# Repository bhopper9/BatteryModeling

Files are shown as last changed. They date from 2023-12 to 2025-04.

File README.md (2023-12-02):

Rensselaer Motorsport Battery Models

This respository currently contains two major projects:

RM26 Project - This was the final battery design for RM26 (2022-2023 competition car).
WIP RM27 Project - This is the most up to date battery design for RM27 (2023-2024 competition car).

Most of the circuits are made using KiCad or LTSpice, both free for download on the internet.

Additional schematics and drawings are from the manufacturer of components or made in Microsoft Visio.

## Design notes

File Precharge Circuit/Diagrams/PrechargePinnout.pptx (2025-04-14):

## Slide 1

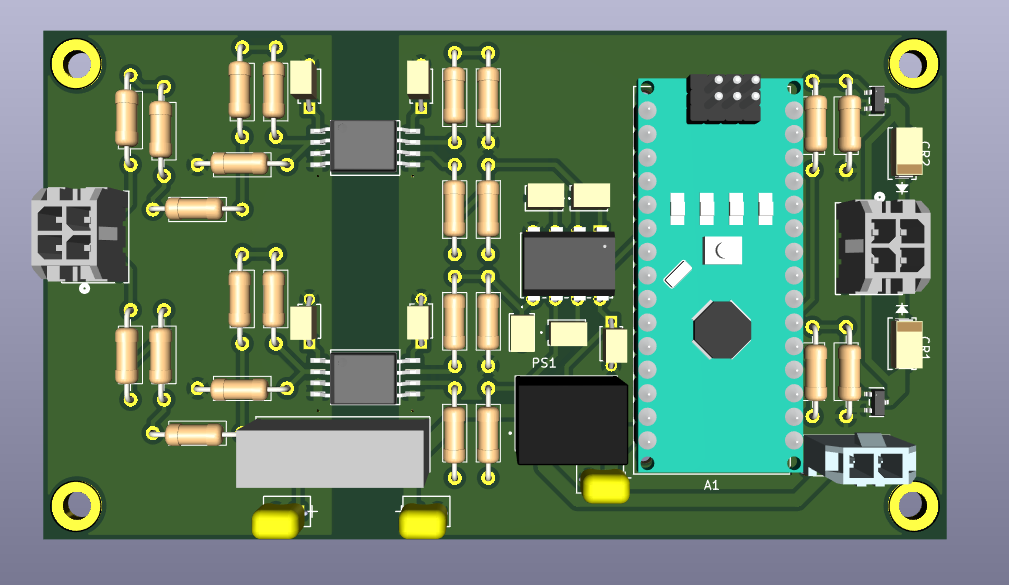
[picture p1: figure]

Relay

SHD IN

VInv

HV GND

VBatt

GND

AIR

V+
(Battery or 12V)

GND

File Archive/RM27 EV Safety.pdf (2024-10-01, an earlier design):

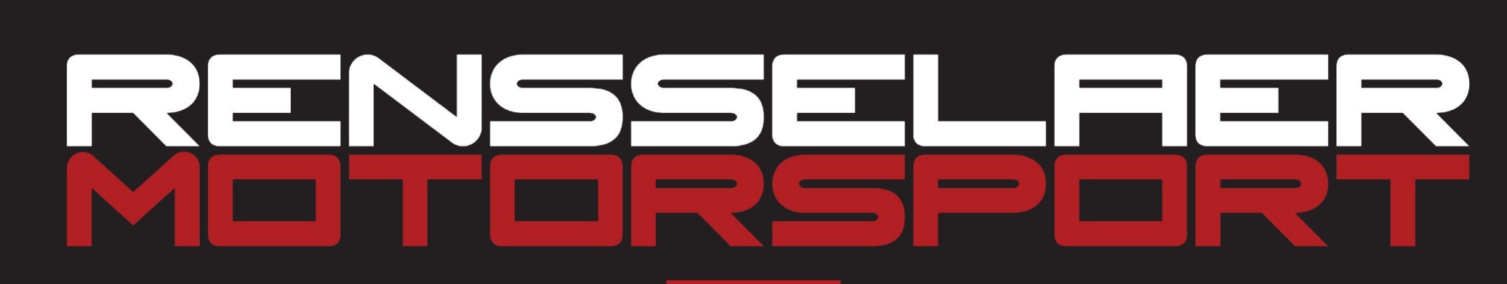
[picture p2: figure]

# Electrical Safety

Sean Trimper - ESO
trimps@rpi.edu - (603)204-0353 December 6, 2023

## - Gain basic knowledge of electrical safety including:

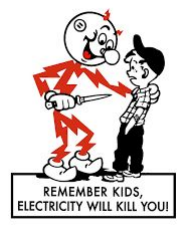
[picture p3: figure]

## a. Battery cells

## b. Powertrain

## c. HV System

## d. LV System

## e. Shutdown system

## f. Equipment

## Goal

- Damaged cells should be reported and handled with extreme care
- Cell wrapping is not just used to change how the cell looks
– | It insulates the positive and negative terminal
– | Even a slight nick in the wrapping will increase the chances of an
| accidental short between the terminals
- Individual cells are capable of high current output
- Misuse or a short between terminals can cause fire or an explosion
- The cells will be hot
- Thermal runaway is when a cell overheats and domino effects the

accumulator (why EV fires are BAD)
- If handling cells, contact ESO

## Battery Cells

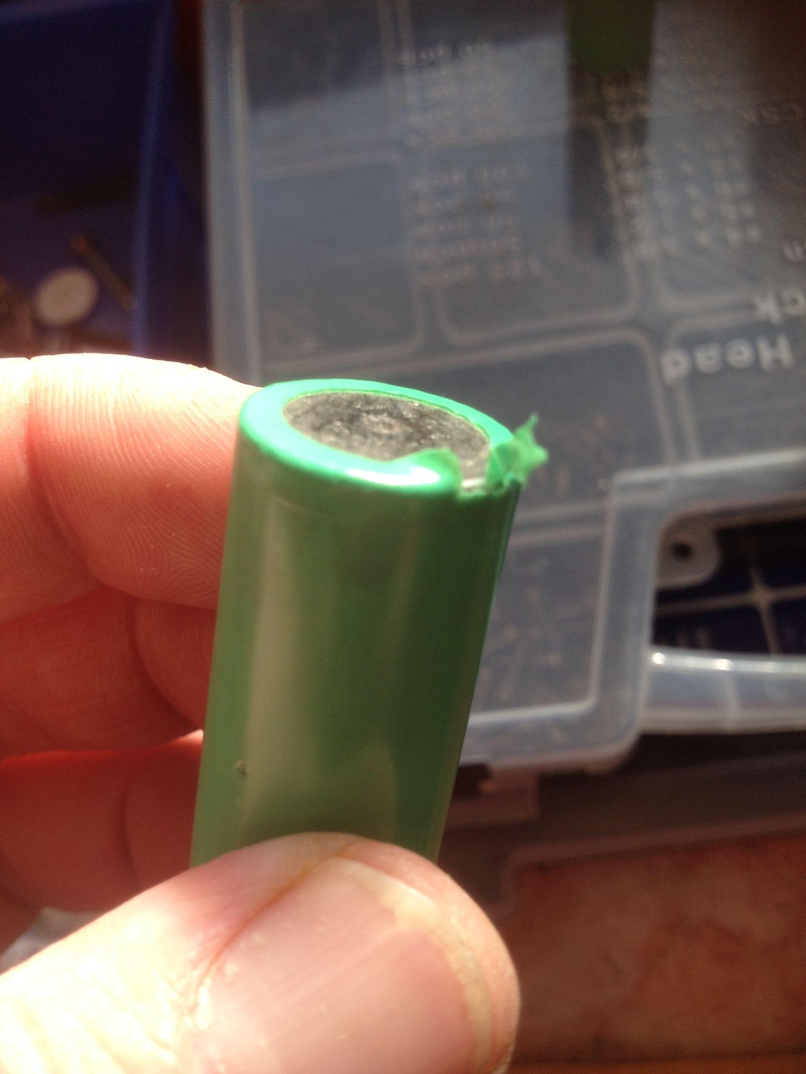
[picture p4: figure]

https://www.osha.gov/sites/default/files/publications/shib011819.pdf

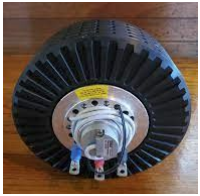
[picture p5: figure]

- In addition to being connected to 400V, the motor is heavy and

moving (and EXPENSIVE)

- The entire motor casing spins FAST
- Even if the motor has stopped moving:
- Ensure power is cut off from the tractive system

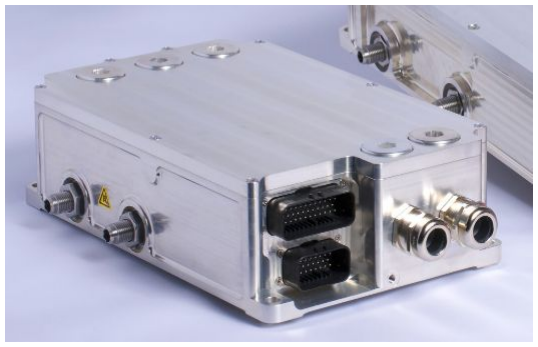
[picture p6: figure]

- Motor will be hot
- The ESC handles many volts and amps
- ESC will be hot
- If handling motor or ESC, contact PT Lead or ESO

## Powertrain

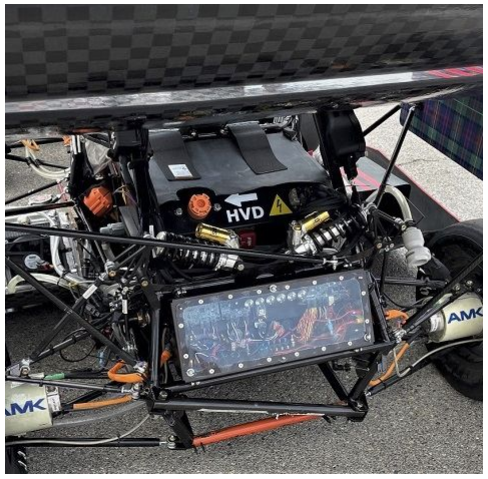
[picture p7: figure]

- There are many built in safety mechanisms within the

accumulator

- If something does go wrong
- High Voltage Disconnect (HVD)
– | There will be an HVD on the car
– | HVD labeled “HVD” and in rear of car
– | PULL MAIN HVD IF DRIVER IN DANGER
- Isolation
– | The battery segments will be isolated from the other
| components in the accumulator
– | Added layer of protection
– | Will make an LED light up colors depending on status

## HV System

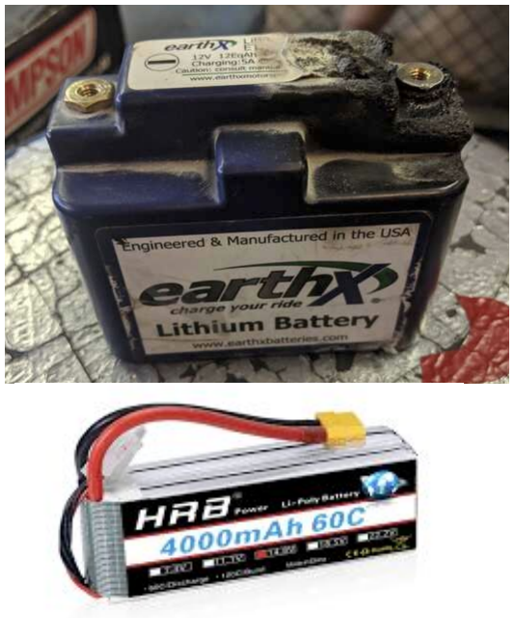
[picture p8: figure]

### - Biggest safety concern is the LV Battery

- Relatively low voltage, but extremely high current
- Ask LV lead or ESO before handeling
- Store in a dry and cool location
- Most common mistake: Shorting cell terminals
– | Overheats and will cause fire
– | THIS HAS HAPPENED TO US BEFORE!!!

### - 12V and 5V systems

- Can short if loose pwr and gnds

– Cover with E-tape

- Has indicator lights

## LV System

## EV Indicator Lights

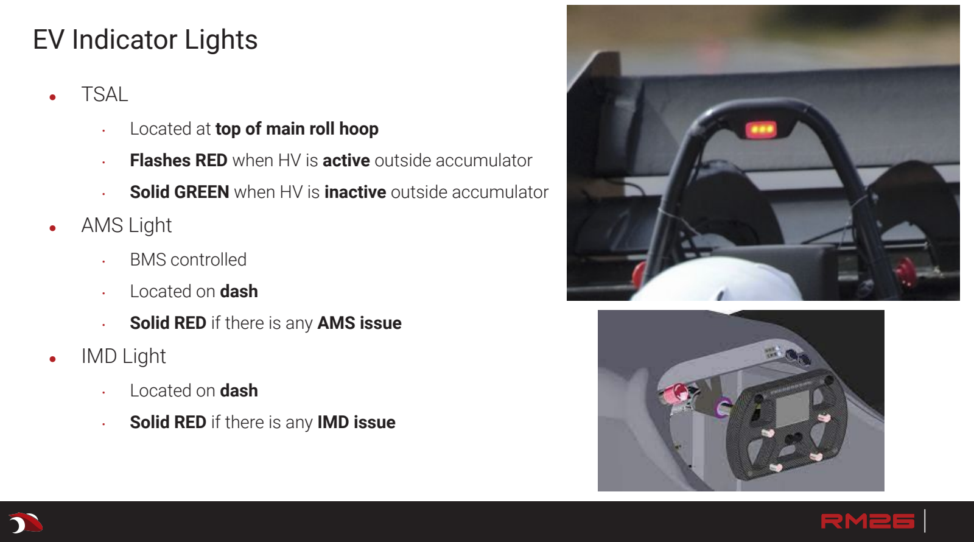
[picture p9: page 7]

- TSAL
- Located at top of main roll hoop
- Flashes RED when HV is active outside accumulator
- Solid GREEN when HV is inactive outside accumulator
- AMS Light
- BMS controlled
- Located on dash
- Solid RED if there is any AMS issue
- IMD Light
- Located on dash
- Solid RED if there is any IMD issue

- The shutdown circuit controls the the accumulators connection

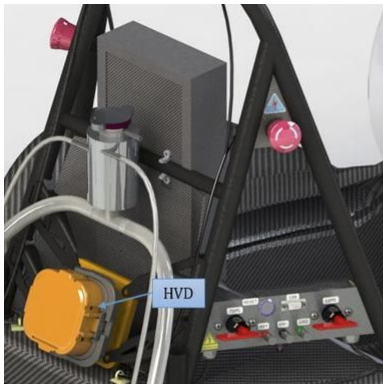
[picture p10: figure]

to the tractive system

- What happens when the shutdown circuit opens?
- 5 separate buttons to open the circuit (turn off the car)
– | LV Master Switch
– | Tractive System Master Switch
– | Cockpit/Left/ Right Shutdown button
- If any of the monitoring systems open the shutdown circuit they

must be reset manually by someone outside of the cockpit

## Shutdown System

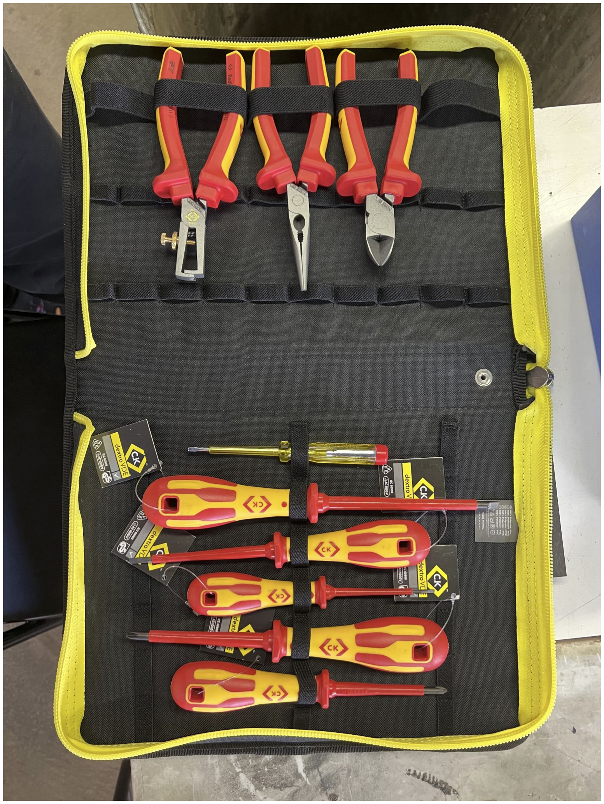
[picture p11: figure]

- HV safety blanket
- Orange Rubber mat
- Reduces chance for short to table
- Use to put accumulator on when working
- HV gloves
- Very thick black rubber gloves
- Use when handling accumulator internals
- HV tools
- Tools with more insulation to protect from higher voltage
- Use when working on accumulator

## Equipment

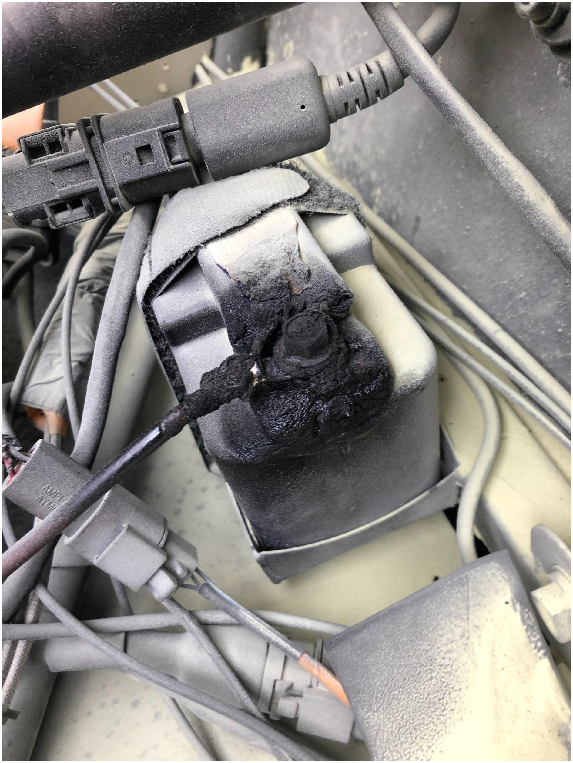
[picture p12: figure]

## Most Common Emergencies

- Accumulator/Car fire
- Due to thermal runaway of overtemp cells
- Ensure driver gets out of car then distance yourself from car
- Isolation error
- Remove HVD
- Put on HV equipment
- Disconnect parts if possible to isolate segments
- Crash/dropped accumulator
- Notify ESO and HV Lead
- Look from afar to ensure no smoke or fire or sparks
- CAREFULLY open and inspect internals for damage

## Questions?

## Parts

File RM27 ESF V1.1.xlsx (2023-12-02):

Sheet: Overview
Instructions |  |  | Status
-All cells for input have an orange background. -Cells, sections and worksheets have an overall status. The status cells have a blue background. -For sections which require an image or schematic, The image should be pasted and located over the specified area. Images should be pasted at a high resolution and then resized. This allows the reader to zoom into the image if more resolution is required. -Where datasheets are requested, a hyperlink to the datasheet from the manufacturer must be provided. -Additional Comments sections are provided throughout for documentation of things which the team feels are not adequately documented in the provided fields. These are optional and do not need to be completed. |  |  | Datasheets | OK
 |  |  | TS Schematics | OK
 |  |  | Accumulator | OK
 |  |  | Precharge/Discharge | BLANK
 |  |  | Charging | OK
 |  |  | Shutdown Circuit | OK
 |  |  | Torque Security | BLANK
 |  |  | Other | OK
 |  |  | Team Name | Rensselaer Motorsport
 |  |  | University | Rensselaer Polytechnic Institute
 |  |  | Competition Year | 2024
 |  |  | Max TS Voltage | 399 | V
 |  |  | Accumulator Fuse | 125 | A
Additional Comments
Template Revision History
Version | Date | Comment
2.2 | 2022-11-03 | Updated for 2023 season.
2.1 | 2021-10-22 | Updated for 2022 season.
2.0 | 2020-11-27 | Multiple updates and bug fixes.

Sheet: Datasheets
Status | OK
Battery Cell |  |  |  | OK
Make |  | Molicel
Model |  | P28A
Nominal Capacity |  | 2.8 | Ahr
Maximum Voltage |  | 4.2 | V
Nominal Voltage |  | 3.6 | V
Minimum Voltage |  | 2.5 | V
Max output current |  | 35 | A
Max continuous current |  | 25 | A
Max Cell temp |  | 60 | C
Cell Chemistry |  | LiNiMnCoO2 (NMC)
Datasheet |  | https://www.molicel.com/wp-content/uploads/INR18650P28A-V1-80093.pdf
SDS |  | https://www.molicel.com/wp-content/uploads/00058ar-Molicel-SDS-Y2020.pdf
Additional Comments
Conductors |  |  |  |  |  |  |  |  | WARNING
Manufacturer | Part Number | Size [mm2] | Voltage [V] | Ampacity [A] | Max Temp [C] | Datasheet |  | Location Used |  | Additional Comments |  |  |  |  | Rules References
Champlain Cable EXRAD | EXRAD® ERGOFLEX ISO 19642-9 EXRAD–EF/EF-TW-50 | 50 | 1000 | 160 | 150 | https://www.champcable.com/wp-content/uploads/2021/06/219.-EXRAD-ERGOFLEX-Shielded-Thin-Wall-Battery-Cable-R3.pdf |  | Accumulator & External High Voltage Routing | OK | Listed Ampacity is at maximum allowed conductor temperature of 150C. At 90C, it is 260 Amps |  |  |  |  | EV.6.2.1 EV.6.2.5 EV.7.3 EV.7.6.4 EV.7.3.2
Team Built | Busbar Collector | 79.6 | N/A | 154 | 90 | N/A |  | Accumulator Segment Poles | OK
Team Built | Busbar |  |  |  |  |  |  |  | WARNING
Fuses |  |  |  |  |  |  |  |  | OK
Manufacturer | Part Number | Voltage [V] | AC/DC | Current [A] | Interrupt [A] | Datasheet |  | Location Used |  | Additional Comments |  |  |  |  | Rules References
Bojack | F2AL250V | 250 | DC | 2 | 1000 | AMS Fuse (https://www.amazon.com/BOJACK-5x20mm-F2AL250V-Fast-Blow-Glass/dp/B07S768TPM) |  | AMS voltage sense | OK |  |  |  |  |  | EV.6.2.1 EV.7.6
Littelfuse | L50QS125.V | 500 | DC | 125 | 50000 | Main Fuse (https://www.mouser.com/datasheet/2/240/L50QS_High_Speed_Fuse_Datasheet-3311429.pdf) |  | Main Fuse | OK
Bel Fuse | 0ADKC5000-BE | 500 | DC | 5 | 20000 | Energy Meter Fuse (https://www.mouser.com/datasheet/2/643/ds_cp_0adkx_series-1960352.pdf) |  | Energy Meter Fuse | OK
Resistors |  |  |  |  |  |  |  |  |  |  |  | OK
Manufacturer | Part Number | Voltage [V] | Resistance [Ω] | Power [W] | Power for 15 sec [W] | Heatsink [°C/W] (Enter "None" if no heatsink) |  |  | Datasheet |  | Location Used |  | Additional Comments |  |  |  | Rules References
Caddock Electronics Inc. | MP925-10.0K-1% | 500 | 10000 | 25 | N/A | None |  |  | MP925 (http://www.caddock.com/Online_catalog/Mrktg_Lit/MP9000_Series.pdf) |  | TSMP | OK |  |  |  |  | EV.6.2.1 EV.6.6 EV.6.8.4
Mouser | 284-HS50-750F | 1250 | 750 | 50 | N/A | None |  |  | 284-HS50-750F (https://www.mouser.com/datasheet/2/303/acl_hs10-1890310.pdf) |  | TSMP | OK
Contactors/Relays |  |  |  |  |  |  |  |  | OK
Manufacturer | Part Number | Voltage [V] | Continuous Current [A] | Max Interrupt Current [A] | Normal State | Datasheet |  | Location Used |  | Additional Comments |  |  |  |  | Rules References
TE Connectivity / Kilovac | LEV200A4NAA | 900 | 500 | 2000 | NO | LEV200A4NAA (https://www.mouser.com/datasheet/2/418/ENG_CS_5-1773450-5_sec7_LEV200_0313_5-1773450-5_Se-1074401.pdf) |  | AIR/Precharge | OK |  |  |  |  |  | EV.6.2.1 EV.6.4 EV.6.6
Panasonic Electric Works | AQZ404 | 400 | 20 | 50 | NC | AQZ404 (https://www3.panasonic.biz/ac/e_download/control/relay/photomos/catalog/semi_eng_pwr1b_aqz40.pdf) |  | Discharge | OK
Connectors |  |  |  |  |  |  |  | OK
Manufacturer | Part Number | Voltage [V] | Ampacity [A] | Wire Size [mm2] | Datasheet |  | Location Used |  | Additional Comments |  |  |  |  | Rules References
Amphenol | RL0-080-1-70* | 1000 | 200 | 50 | RLO-080-1-70* (https://www.amphenol-industrial.com/images/datasheets/IDS-67%20RADLOK.pdf) |  | Accumulator Segments | OK | Maintenance Plug, Connector |  |  |  |  | EV.6.2.1 EV.6.10 EV.7.3.4
Amphenol | RL9-100-202F1 | 1000 | 200 | 50 | RL9-100-202F1 (https://www.amphenol-industrial.com/images/datasheets/IDS-67%20RADLOK.pdf) |  | Accumulator Segments | OK | Maintenance Plug, Pin
Amphenol | MSDM5002 | 690 | 500 | 50 | MSDM5002 (https://www.mouser.com/datasheet/2/18/1/msd_m_xxxx_rev_a_cdr-1853453.pdf) |  | HVD | OK
Insulating Materials |  |  |  |  |  |  |  |  |  | BLANK
Manufacturer | Part Number | Thickness [mm] | Dielectric strength [V/mm] | Voltage Rating [V] | Max Temp [C] | Flammability Rating | Datasheet |  | Location Used |  | Additional Comments |  |  |  |  | Rules References
 |  |  |  |  |  |  |  |  |  | BLANK |  |  |  |  |  | EV.6.2.1 EV.6.2.2.a EV.6.2.3 EV.6.4.4 EV.7.2 EV.7.5.5.a

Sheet: TS Schematics
Status | OK
Tractive System Schematic |  |  |  |  | Accumulator TS Schematic |  |  |  | Additional Comments
Vehicle Tractive System Schematic Shows |  |  |  | OK | Accumulator TS Schematic Shows |  |  | OK
Rules References |  |  |  |  | Rules References
 |  | Shows details of all TS circuits outside of accumulator | TRUE | OK |  | Details of all TS circuits within accumulator | TRUE | OK
 |  | Accumulator is shown as a single element (without internal details) | TRUE | OK |  | All wire gauges labeled | TRUE | OK
 |  | All wire gauges labeled | TRUE | OK |  | All fuses labeled with ampacity | TRUE | OK
 |  | All fuses labeled with ampacity | TRUE | OK |  | All wires > 150mm have a fuse within the first 150mm from the source | TRUE | OK
 |  | All wires > 150mm have a fuse within the first 150mm from the source | TRUE | OK |  | Fuse locations represent physical location | TRUE | OK
 |  | Fuse locations represent physical location | TRUE | OK |  | Connectors labeled with Make/Model | TRUE | OK
 |  | Enclosures shown | TRUE | OK |  | Standard schematic symbols used | TRUE | OK
 |  | Connectors labeled with Make/Model | TRUE | OK |  | All text is readable (zooming is allowed) | TRUE | OK
 |  | Standard schematic symbols used | TRUE | OK | EV.6.4 | AIRs | TRUE | OK
 |  | All text is readable (zooming is allowed) | TRUE | OK | EV.6.3 | Maintenance plugs | TRUE | OK
EV.6.8 |  | TSMPs | TRUE | OK |  | Cells (details of all intercell connections may be abstracted) | TRUE | OK
 |  | Motor Controller | TRUE | OK |  | Accumulator Indicator | TRUE | OK
 |  | Motor | TRUE | OK
EV.6.8.5 |  | TSMPs not fused | TRUE | OK
Must be shown on at least one schematic |  |  |  | OK
Rules References
EV.8.6 |  | IMD | TRUE | OK
EV.6.5 |  | HVD | TRUE | OK
EV.6.6 |  | Precharge | TRUE | OK
EV.6.6 |  | Discharge | TRUE | OK
EV.4.2.3; EV.6.1.3 |  | Energy Meter | TRUE | OK
EV.6.6.1.c |  | Precharge is not fused | TRUE | OK
EV.6.6.1.c |  | Discharge is not fused | TRUE | OK

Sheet: Accumulator
Status | OK
Segment-to-Segment Connection |  |  |  | Series |  | OK
Maximum TS Voltage |  |  |  | 399 | V | OK
Nominal TS Voltage |  |  |  | 342 | V
Total Cells |  |  |  | 570
Segment Data |  |  |  |  |  |  |  |  | OK | BMS |  |  |  |  | OK | Maintenance Plugs |  |  |  | OK | Insulating Materials |  |  |  | BLANK | Additional Comments
Cell Connection Order |  |  | Parallel then Series |  |  |  |  |  | OK | BMS Type |  |  | Centralized |  | OK | Connector |  | Amphenol RL0-080-1-70* |  | OK | Between cells and accum. container |  |  |  | BLANK | No wires >150mm (no fuses for those wires needed).
Segment | Parallel cells | Series cells | Temp Sensors | Accumulator Number | Max Voltage [V] |  | Segment Energy [MJ] |  |  | BMS Source |  |  | Purchased |  | OK | Ampacity |  | 200 | A | OK | Voltage Rating |  | #N/A | V | BLANK
 |  |  |  |  |  |  |  |  |  | Make | Orion | Model | BMS2 156-Cell |  | OK | Segment Fuse |  |  |  |  | Temperature Rating |  | #N/A | C | BLANK
1 | 6 | 19 | 25 | 1 | 79.8 |  | 4.826304 |  | OK | Galvanic Isolation TS to GLV |  |  | 1500 | V | OK | Segment Fuse Ampacity |  | #N/A | A |  | On top of cells |  |  |  | BLANK
2 | 6 | 19 | 25 | 1 | 79.8 |  | 4.826304 |  | OK | Galvanic Isolation between segments |  |  | 2500 | V | OK | AIR |  |  |  |  | Voltage Rating |  | #N/A | V | BLANK
3 | 6 | 19 | 25 | 1 | 79.8 |  | 4.826304 |  | OK | Galvanic Isolation device |  |  |  |  |  | Make/Model |  | TE Connectivity / Kilovac LEV200A4NAA |  | OK | Temperature Rating |  | #N/A | C | BLANK
4 | 6 | 19 | 25 | 1 | 79.8 |  | 4.826304 |  | OK | Gavlanic Isolation device datasheet |  |  |  |  |  | Contact Voltage Rating |  | 900 | V | OK | Separating AIR and Fuse from cells |  |  |  | BLANK
5 | 6 | 19 | 25 | 1 | 79.8 |  | 4.826304 |  | OK | Voltage Sense Leads |  |  |  |  |  | Max switching current |  | 2000 | A |  | Voltage Rating |  | #N/A | V | BLANK
6 |  |  |  |  | 0 |  | 0 |  |  | Max Sense Lead Length |  |  | 90 | cm | OK | Max continuous current |  | 500 | A | OK | Temperature Rating |  | #N/A | C | BLANK
7 |  |  |  |  | 0 |  | 0 |  |  | Sense Lead Overcurrent Protection Device |  |  | Bojack F2AL250V |  | OK | Main Fuse
8 |  |  |  |  | 0 |  | 0 |  |  | Overcurrent Location |  |  | BMS PCB |  | OK | Main Fuse |  | Littelfuse L50QS125.V |  | OK
9 |  |  |  |  | 0 |  | 0 |  |  | Overcurrent Other Location |  |  |  |  |  | Main fuse ampacity |  | 125 | A
10 |  |  |  |  | 0 |  | 0 |  |  | Overcurrent Voltage Rating |  |  | 250 |  | OK | Main fuse voltage |  | 500 | V | OK
11 |  |  |  |  | 0 |  | 0 |  |  | Temperature Sensors
12 |  |  |  |  | 0 |  | 0 |  |  | Temp Sensor Location |  |  | On cell terminal |  | OK
13 |  |  |  |  | 0 |  | 0 |  |  | Distance to cell terminal |  |  |  | mm
14 |  |  |  |  | 0 |  | 0 |  |  | Cells sensed per sensor |  |  | 1 | cells | OK
15 |  |  |  |  | 0 |  | 0 |  |  | Thermal Contact material used |  |  | 6
16 |  |  |  |  | 0 |  | 0 |  |  | Thermal contact material datasheet |  |  | Silicon Rubber Sheet (https://www.mcmaster.com/1272N15/) |  | OK
17 |  |  |  |  | 0 |  | 0 |  |  | Thermal contact material conductivity |  |  | 5 | W/(m∙K) | OK
18 |  |  |  |  | 0 |  | 0 |  |  | Thermal contact material thickness |  |  | 0.5 | mm | OK
 |  |  |  |  |  |  |  |  |  | Percent of cells sensed |  |  | 21.805 | % | OK
Picture of Maintenance Plugs |  |  |  |  |  |  |  |  | Picture of Cell Connections |  |  |  |  |  |  |  | Picture of Temperature Sensor Location |  |  |  |  |  | Picture of Fuse and AIR Separation from Cells |  |  |  |  | Picture of Segment Insulation between Cell Terminals and Sides of Accumulator Container |  | Picture of Insulation on Top of Segment
Maintenance Plug(s) Picture Shows |  |  |  |  |  |  | BLANK |  | Cell Connections Picture Shows |  |  |  |  |  | BLANK |  | Temperature Sensor Picture Shows |  |  |  |  | BLANK | Fuse and AIR Separation Picture Shows |  |  |  | BLANK | Segment Insulation Picture Shows | BLANK | Segment Insulation Picture Shows | BLANK
Unique Configuration of plugs |  |  |  |  |  |  | BLANK |  | Bolted connection have positive locking |  |  |  |  |  | BLANK |  | Temp sensor in direct contact with terminal or busbar |  |  |  |  | BLANK | Fuse and AIR are separated from cells |  |  |  | BLANK | Insulation between cells and accumulator container | BLANK | Insulation on top of cells (air not acceptable) | BLANK
Non-conductive on un-necessary surface |  |  |  |  |  |  | BLANK |  | location of parallel cell overcurrent for parallel cells |  |  |  |  |  | BLANK |  | Distance from sensor to cell negative terminal |  |  |  |  | BLANK | Additional Comments |  |  |  | Rules References | Additional Comments | Rules References | Additional Comments | Rules References
Positive Locking |  |  |  |  |  |  | BLANK |  | Additional Comments |  |  |  |  |  | Rules References |  | Additional Comments |  |  |  |  | Rules References |  |  |  |  | EV.6.4.4 |  | EV.6.2.2.a EV.6.2.3 |  | EV.6.2.2.a EV.6.2.3
Additional Comments |  |  |  |  |  |  | Rules References |  |  |  |  |  |  |  | EV.7.4.1 EV.7.4.3 |  |  |  |  |  |  | EV.8.5
 |  |  |  |  |  |  | EV.6.3
Parallel Cell Fusing |  |  |  |  | WARNING | Rules Referenes
Source |  |  | Team Designed |  | OK | EV.7.6.3 EV.7.6.5
Make/Model
Continuous Current |  |  | #N/A | A
Continuous Current |  |  | 67 | A | OK
Test Data Summary
Tests at current 1 |  |  | 0 |  | WARNING
Tests at current 2 |  |  | 0 |  | WARNING |  | #NUM! | 67
Tests at current 3 |  |  | 0 |  | WARNING |  | #NUM! | 67
Tests at current 4 |  |  | 0 |  | WARNING
See Fusible Link Testing Guideline on FSAEOnline.com
Testing | Current [A] | Time to blow [s]
Test 1
Test 2
Test 3
Test 4
Test 5
Test 6
Test 7
Test 8
Test 9
Test 10
Test 11
Test 12
Test 13
Test 14
Test 15
Test 16

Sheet: PrechargeDischarge
Status | BLANK
Precharge |  |  |  | BLANK | Discharge |  |  | OK | TSMP |  |  | OK | Rules References
Resistor |  | Mouser 284-HS50-750F |  | OK | Resistor | Mouser 284-HS50-750F |  | OK | Resistor | Caddock Electronics Inc. MP925-10.0K-1% |  | OK | EV.6.8.4
# parallel |  | 1 |  | OK | # parallel | 1 |  | OK | # parallel | 1 |  | OK
# series |  | 1 |  | OK | # series | 1 |  | OK | # series | 1 |  | OK
Resistance |  | 750 | Ohms |  | Resistance | 750 | Ohms |  | Resistance | 10000 | Ohms | OK
Cont power |  | 50 | W |  | Cont power | 50 | W |  | Cont power | 25 | W | OK
power @15 sec |  | #VALUE! | W |  | power @15 sec | #VALUE! | W | #VALUE! | Voltage | 500 | V | OK
Voltage |  | 1250 | V | OK | Voltage | 1250 | V | OK
Bus Capacitance |  | 0.44 | mF | OK | Peak power | 212.268 | W
End of precharge |  | Time |  | OK | Peak current | 0.53 | A
time |  | 3 | sec | OK | Discharge time (to 60V) | 0.625223562 | s
delta V |  |  | V |  | Relay | Panasonic Electric Works AQZ404 |  | OK
ending ratio |  |  | % |  | Relay voltage rating | 400 | V | OK
Peak power |  | 212.268 | W |  | Relay current rating | 20 | A | OK
Peak current |  | 0.53 | A |  | Normal State | NC |  | OK
time to 90% |  | 0.76 | sec |  | Rules References
Precharge Res Energy to 90% |  | 34.67 | J |  | EV.6.6
Average Power |  | 45.6 | W
Relay |  |  |  | BLANK
Relay voltage rating |  | #N/A | V | #N/A
Relay current rating |  | #N/A | A | #N/A
Additional Comments

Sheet: Charging
Status | OK
Charger |  |  |  |  | OK | Additional Comments
Make |  |  | Elcon |  | OK
Model |  |  | 6.6kW HK-J CAN UHF |  | OK
Datasheet |  |  | Elcon Charger (https://www.electricmotorsport.com/ev-parts/chargers/multi-chemistry/elcon-6-6kw-hk-j-can-uhf-charger.html) |  | OK
Input Voltage |  |  | 85~265V | V | OK
Input Current |  |  | 32 | A | OK
Output Voltage |  |  | 170-650 | V | OK
Output Current |  |  | 12 | A | OK
Power |  |  | 6.6 | kW | OK
Input to Output isolation |  |  | 2000 VAC 10 mA |  | OK
Charging Tractive System Schematic |  |  |  |  |  |  | Charging Shutdown Circuit
Charging Tractive System Schematic Shows |  |  |  |  |  | BLANK | Charging Shutdown Circuit Shows |  |  | BLANK
Rules References |  |  |  |  |  |  | Rules References
 |  | Fuse |  |  |  | BLANK | EV.9.3 | IMD Control and Powerstage |  | BLANK
 |  | Connectors |  |  |  | BLANK | EV.9.3 | AMS |  | BLANK
 |  | Wire Gauge |  |  |  | BLANK | EV.9.2.7 | Charger Shutdown Button | TRUE | OK
EV.9.4 |  | IMD |  |  |  | BLANK | EV.9.4 | AIRs |  | BLANK
EV.9.4.2 |  | AIRs |  |  |  | BLANK |  | Charge Connector Interlock |  | BLANK
EV.9.2.6 |  | TSMPs |  |  |  | BLANK |  | Charge Control (CAN, Enable, etc.) |  | BLANK
Additional Comments |  |  |  |  |  |  | Additional Comments

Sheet: Shutdown Circuit
Status | OK
IMD |  |  |  |  | OK | BSPD |  |  |  | OK
Rules Reference |  |  | EV.8.6 |  |  | Rules Reference |  | EV.8.7
Make/Model |  |  | Bender IR155-3203 |  | OK | Current Sensor Make/Model |  | DHAB S/124 |  | OK
Setpoint |  |  | 500 | kΩ | OK | Current Sensor Datasheet |  | https://www.lem.com/sites/default/files/products_datasheets/dhab_s_124.pdf |  | OK
 |  |  |  |  |  | Trip Current |  | 14.6 | A | OK
 |  |  |  |  |  | Sensor Output @ Trip Current |  | 2.99 | V | OK
 |  |  |  |  |  | Accuracy @ Trip Current |  | 0.4 | A | OK
Shutdown Circuit Schematic
Shutdown Circuit Schematic Shows |  |  |  |  |  |  |  | BLANK |  | BSPD System Schematic Shows |  | OK
Rules References
EV.8.9 |  | GLVMS |  |  |  |  | TRUE | OK |  | BSPD Current Sensor input open/short circuit protection | TRUE | OK
EV.8.9 |  | TSMS |  |  |  |  | TRUE | OK |  | BSPD Brake Position input open/short circuit protection | TRUE | OK
EV.8.10 |  | 2 Side Shutdown Buttons |  |  |  |  | TRUE | OK |  | Shutdown circuit powerstage | TRUE | OK
EV.8.10 |  | 1 Cockpit Shutdown Button |  |  |  |  | TRUE | OK |  | Additional Comments | Rules References
T.3.2 |  | Brake Over Travel Switch (BOTS) |  |  |  |  | TRUE | OK |  |  | EV.8.7
EV.8.8 |  | Inertia Switch |  |  |  |  | TRUE | OK
EV.8.3 |  | AMS |  |  |  |  | TRUE | OK
EV.8.6 |  | IMD |  |  |  |  | TRUE | OK
EV.8.7 |  | BSPD |  |  |  |  | TRUE | OK
EV.6.5.2 |  | HVD Interlock |  |  |  |  | TRUE | OK |  | TSAL Schematic
EV.8.1.4 |  | IMD, AMS, BSPD have independent power stages |  |  |  |  |  | BLANK
EV.5.1.3 |  | Outboard Wheel Motor Interlocks |  |  |  |  | FALSE | WARNING
 |  | GLV Battery |  |  |  |  |  | BLANK
 |  | GLV Fuse |  |  |  |  |  | BLANK
 |  | Wire Gauge |  |  |  |  |  | BLANK
EV.8.1.2 |  | Precharge Contactor coil |  |  |  |  |  | BLANK
EV.8.1.2 |  | Positive AIR coil |  |  |  |  |  | BLANK
EV.8.1.2 |  | Negative AIR coil |  |  |  |  |  | BLANK
 |  | Discharge Contactor coil |  |  |  |  |  | BLANK
EV.8.9.1; EV.8.9.3 |  | TSMS is last switch |  |  |  |  | TRUE | OK
EV.8.9.1; EV.8.9.2 |  | GLVMS is first switch |  |  |  |  | TRUE | OK
 |  | Uses proper electrical schematic symbols |  |  |  |  | TRUE | OK
 |  | Labels/text are readable (zooming in is acceptable) |  |  |  |  | TRUE | OK
EV.6.10 |  | Interlocks on TS connectors outside of an enclosure |  |  |  |  | TRUE | OK
Additional Comments |  |  |  |  |  |  | Rules References
SIM101MLQ used for IMD as legal by updated FSAE notification about extra legal IMDs. |  |  |  |  |  |  | EV.8.1 EV.8.2
 |  |  |  |  |  |  |  |  |  | TSAL Schematic Shows |  | BLANK
 |  |  |  |  |  |  |  |  |  | TSAL controlled by >60V present in TS |  | BLANK
 |  |  |  |  |  |  |  |  |  | TSAL powered by GLV |  | BLANK
 |  |  |  |  |  |  |  |  |  | TSAL flashes red when HV present and solid green when not |  | BLANK
 |  |  |  |  |  |  |  |  |  | Additional Comments | Rules References
 |  |  |  |  |  |  |  |  |  |  | EV.6.9

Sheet: Torque Security
Status | BLANK
APPS Sensor Transfer function |  |  |  | BLANK | Torque Control Path Security Checks |  |  |  |  |  |  |  |  | BLANK
Rules Reference |  | T.4.2.3
Position | APPS1 Output [V] |  | APPS2 Output [V] |  | Source Device | Destination Device | Communication | Redundant | Out Of Range | Correlation | Checksum | Timeout | Other |  | Additional Comments
0% |  |  |  | BLANK
20% |  |  |  | BLANK | APPS |  |  |  |  |  |  |  |  | BLANK
40% |  |  |  | BLANK
60% |  |  |  | BLANK
80% |  |  |  | BLANK
100% |  |  |  | BLANK

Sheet: Other
Status | OK
Motor Controller |  |  |  | OK | Motor |  |  | OK
Make |  | Rinehart Motion Systems LLC |  | OK | Make |  | Emrax | OK
Model |  | PM100DX |  | OK | Model |  | 228 HV CC | OK
Datasheet |  | PM100DX (https://stealthev.com/wp-content/uploads/2019/06/PM100-Spec-Sheet.pdf) |  | OK | Datasheet |  | Emrax 228 (https://emrax.com/wp-content/uploads/2020/03/emrax_228_technical_data_table_graphs_5.4.pdf) | OK
Galvanic Isolation between TS and control |  | 1000 | V | OK
Picture of Energy Meter download connector on car to prove compliance with EV.4.2.2
Energy Meter Download Picture Shows |  |  |  |  |  | BLANK
Energy Meter Download Connector |  |  |  |  |  | BLANK
Additional Comments

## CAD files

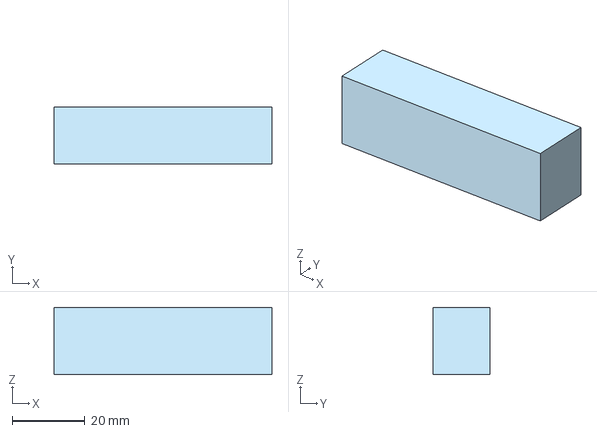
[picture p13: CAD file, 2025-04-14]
Precharge Circuit/Blake_Relay.step
59.9 x 15.7 x 18.5 mm

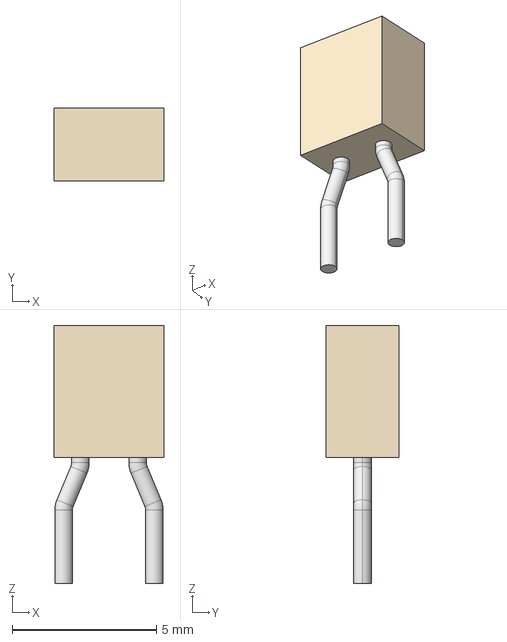
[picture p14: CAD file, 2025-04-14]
Precharge Circuit/Parts/100pFCap/CAP_C315C_MOLDED_KEM.step
3.81 x 2.54 x 8.94 mm

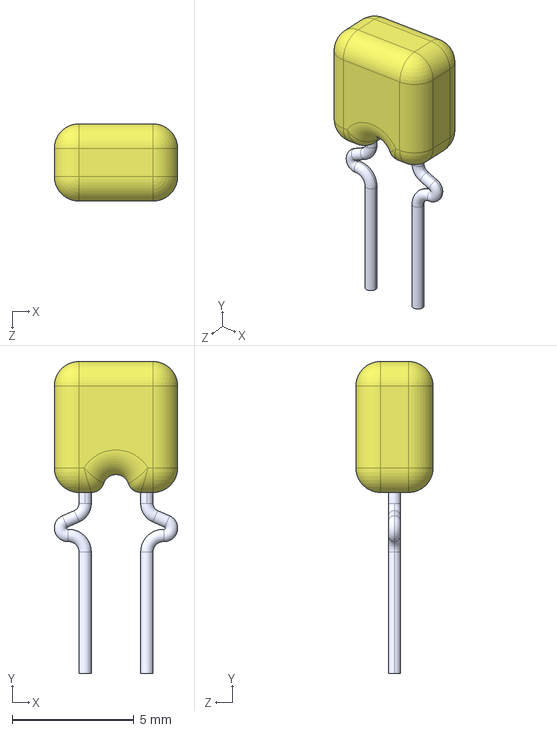
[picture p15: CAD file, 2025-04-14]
Precharge Circuit/Parts/10uFCap/C324C106K3R5TA.STEP
5.08 x 12.8 x 3.18 mm

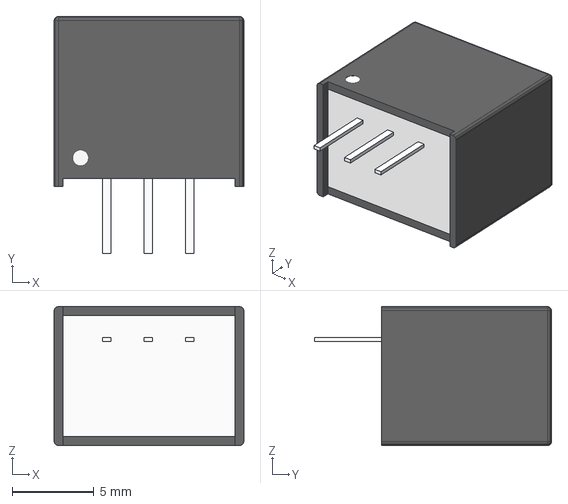
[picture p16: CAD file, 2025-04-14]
Precharge Circuit/Parts/12-5V Converter/R-78E5.0-0.5.step
11.6 x 14.5 x 8.51 mm

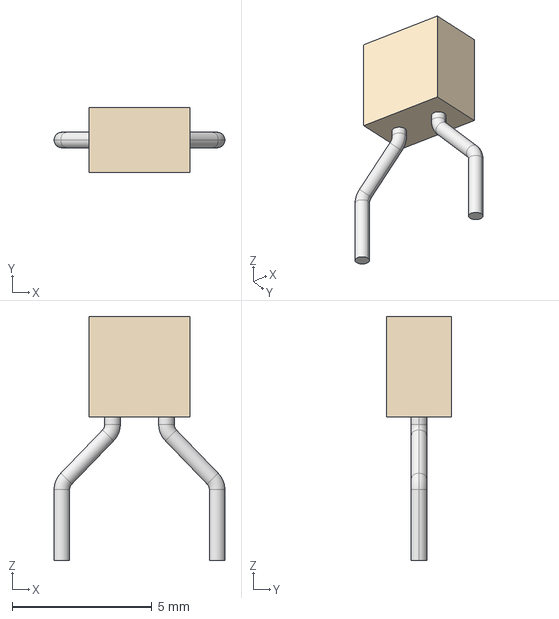
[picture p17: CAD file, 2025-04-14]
Precharge Circuit/Parts/1uFCap/K104K10X7RF5UH5_VIS.step
6.12 x 2.31 x 8.74 mm

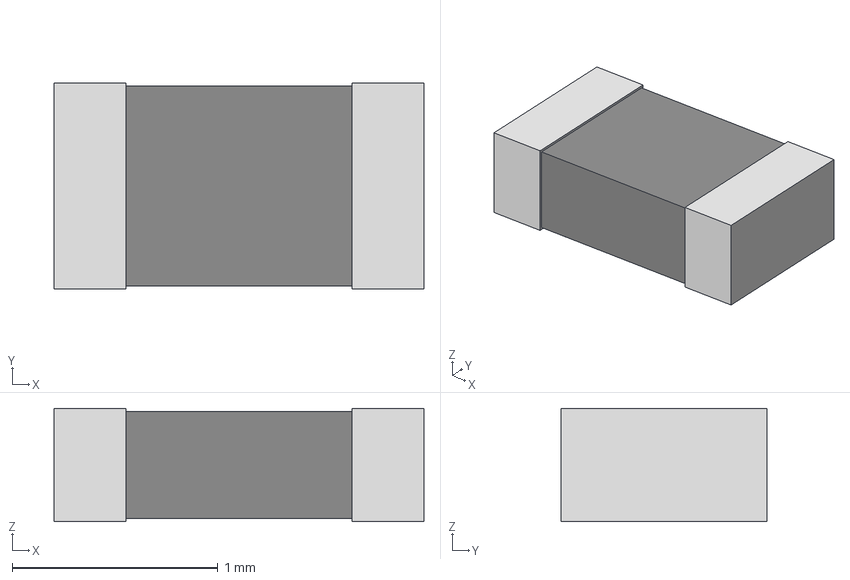
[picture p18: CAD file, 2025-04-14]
Precharge Circuit/Parts/200k Resistor/RES_0816_SUS.step
1.80 x 1.00 x 0.55 mm

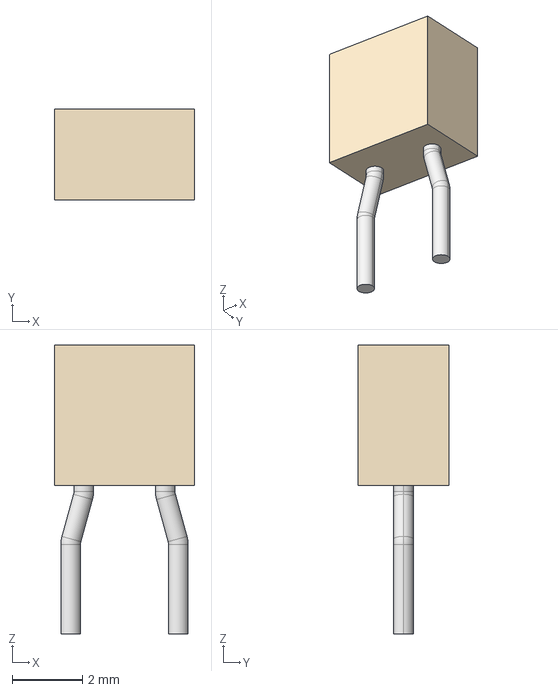
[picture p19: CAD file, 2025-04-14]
Precharge Circuit/Parts/330pFCap/CAP_K-SERIES_15-L2_VIS.step
3.99 x 2.59 x 8.20 mm

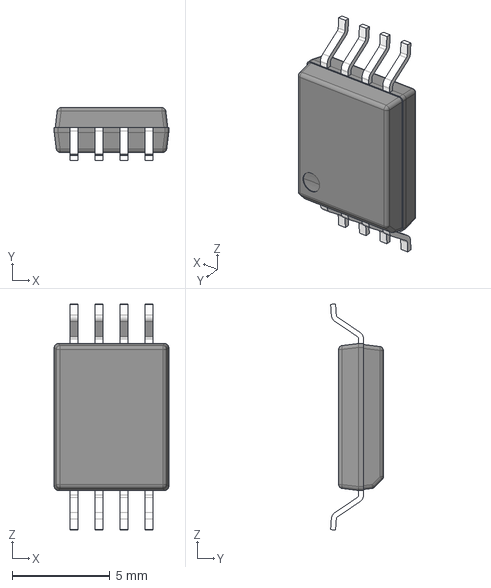
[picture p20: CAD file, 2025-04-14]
Precharge Circuit/Parts/AMC 1351/DWV0008A.stp
5.85 x 2.70 x 11.5 mm
BODY-SOIC
LEAD-DWV0008A x 8

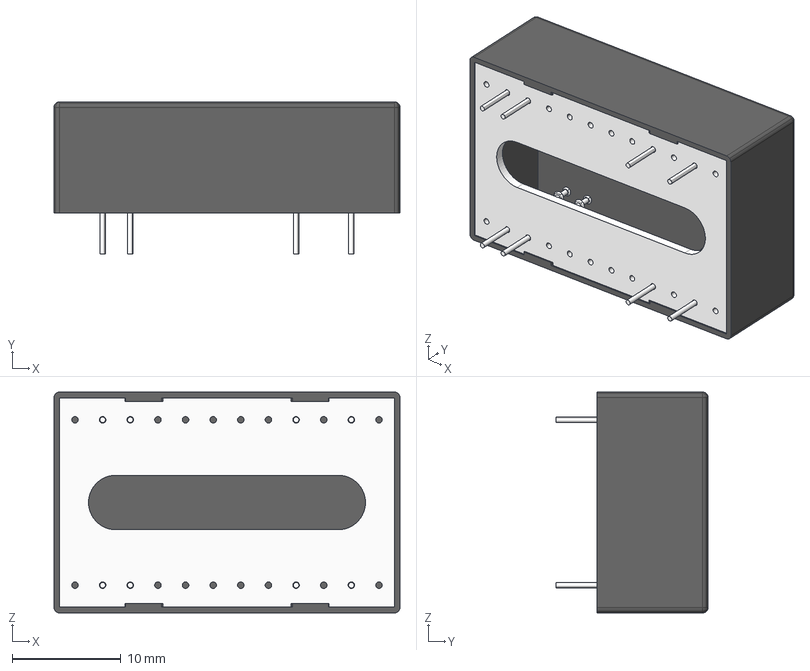
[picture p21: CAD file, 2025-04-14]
Precharge Circuit/Parts/Battery-12V/REC5-1212SRW_H6_A.step
31.8 x 14.0 x 20.3 mm

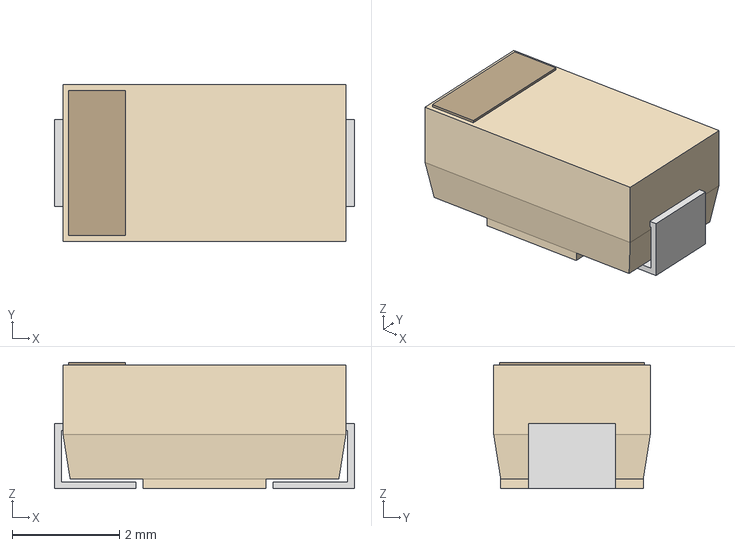
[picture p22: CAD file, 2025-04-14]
Precharge Circuit/Parts/Flyback Diode/SMA_DIO.step
5.59 x 2.92 x 2.35 mm

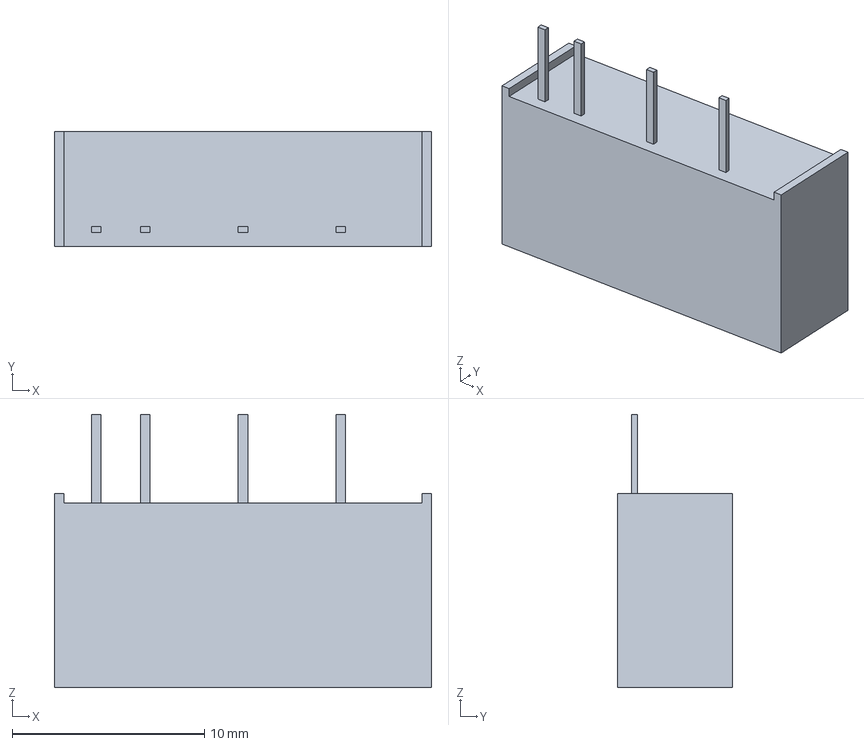
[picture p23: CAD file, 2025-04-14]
Precharge Circuit/Parts/Isolating DC-DC Converter/tea1e_3d_drawing.stp
19.6 x 6.00 x 14.2 mm

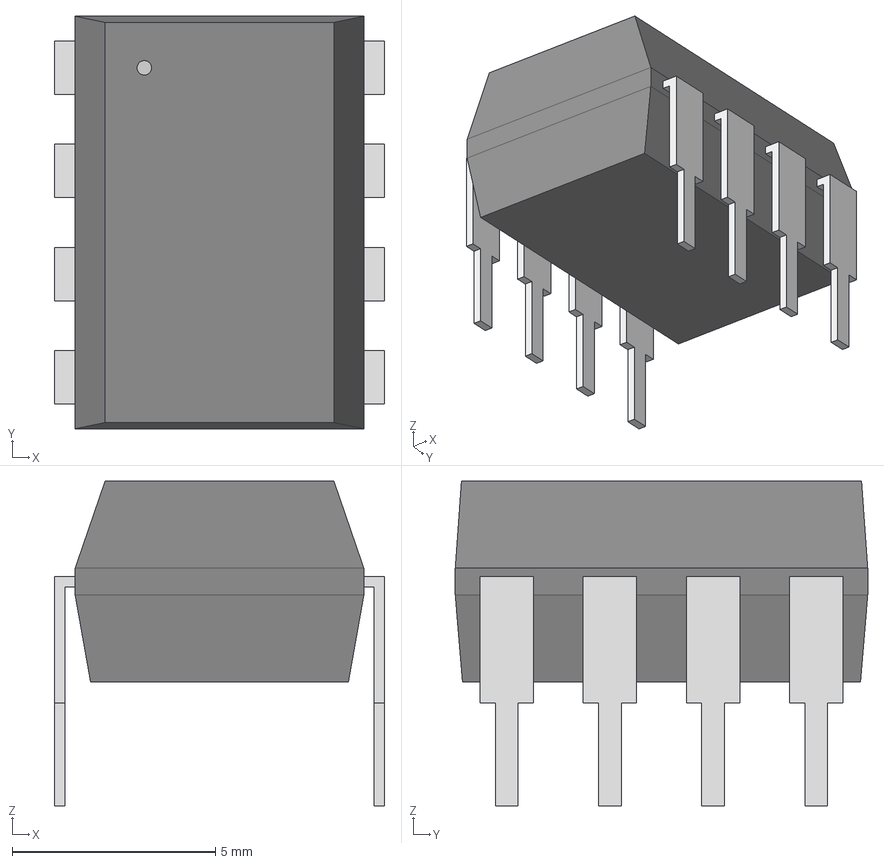
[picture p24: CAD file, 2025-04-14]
Precharge Circuit/Parts/OP284/N_8_ADI.step
8.13 x 10.2 x 8.00 mm

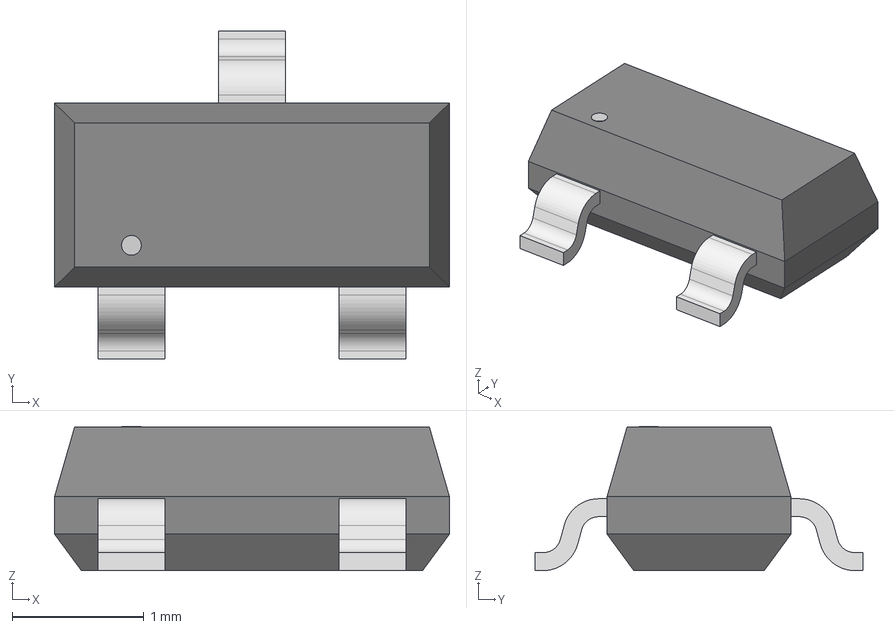
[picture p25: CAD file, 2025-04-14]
Precharge Circuit/Parts/RelayFet/SOT23_DIO.step
3.00 x 2.49 x 1.09 mm

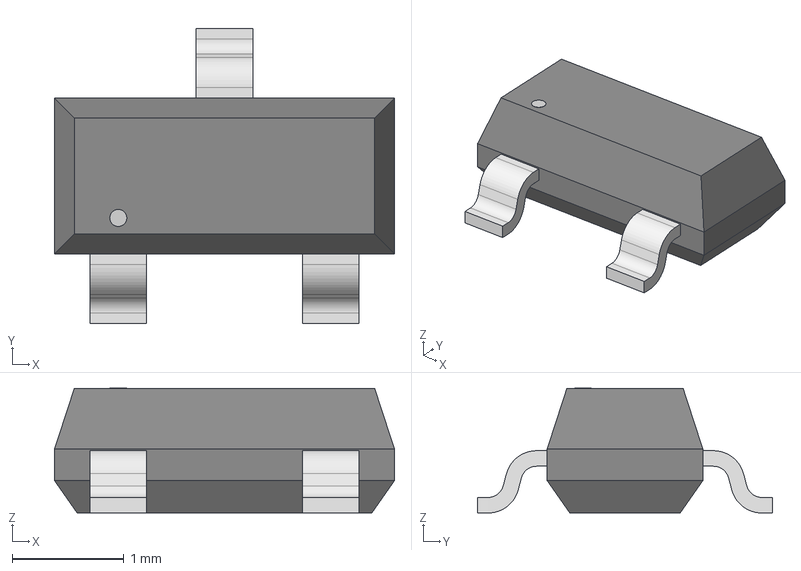
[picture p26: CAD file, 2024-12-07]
Precharge Circuit/Relay Driver IC/SOT-23_TO-236_318_AT_OSI.step
3.05 x 2.64 x 1.12 mm

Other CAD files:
Precharge Circuit/Arduino Nano-STEP.STEP
Precharge Circuit/Arduino v5.step
Precharge Circuit/Parts/Connectors/436500200.stp
Precharge Circuit/Parts/Connectors/430450401.stp
Precharge Circuit/Parts/Connectors/436500300.stp
Precharge Circuit/Parts/Isolation Amplifier/DWV0008A.stl
Precharge Circuit/Parts/MolexMicrofit/430450428.stp
Precharge Circuit/Parts/MolexMicrofit/436500228.stp

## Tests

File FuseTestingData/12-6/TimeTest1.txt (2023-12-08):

09,0.0000,
5710,0.0000,
5711,0.0000,
5712,0.0000,
5714,0.0000,
5715,0.0000,
5716,0.0000,
5718,0.0000,
5719,0.0000,
5720,0.0000,
5722,0.0000,
5723,0.0000,
5724,0.0000,
5725,0.0000,
5726,0.0000,
5727,0.0000,
5729,0.0000,
5730,0.0000,
5731,0.0000,
5732,0.0000,
5733,0.0000,
5734,0.0000,
5736,0.0000,
5737,0.0000,
5738,0.0000,
5739,0.0000,
5740,0.0000,
5741,0.0000,
5742,0.0000,
5744,0.0000,
5745,0.0000,
5746,0.0000,
5747,0.0000,
5748,0.0000,
5749,0.0000,
5751,0.0000,
5752,0.0000,
5753,0.0000,
5754,0.0000,
5755,0.0000,
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

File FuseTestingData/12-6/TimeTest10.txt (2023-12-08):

7838,0.0000,
7839,0.0000,
7840,0.0000,
7841,0.0000,
7843,0.0000,
7844,0.0000,
7845,0.0000,
7846,0.0000,
7847,0.0000,
7848,0.0000,
7851,0.0000,
7852,0.0000,
7853,0.0000,
7854,0.0000,
7855,0.0000,
7856,0.0000,
7858,0.0000,
7859,0.0000,
7860,0.0000,
7861,0.0000,
7862,0.0000,
7863,0.0000,
7865,0.0000,
7866,0.0000,
7867,0.0000,
7868,0.0000,
7869,0.0000,
7870,9.9406,
7872,8.7859,
7873,7.9324,
7874,0.0000,
7875,0.0000,
7876,8.8612,
7877,8.7357,
7879,8.6604,
7880,8.8110,
7881,8.7357,
7882,8.5851,
7883,8.8612,
7884,8.8612,
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

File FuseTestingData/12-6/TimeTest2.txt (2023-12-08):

18962,0.0000,
18964,0.0000,
18965,0.0000,
18966,0.0000,
18967,0.0000,
18969,0.0000,
18970,0.0251,
18971,0.0753,
18972,0.1004,
18974,0.1255,
18975,0.3514,
18976,0.0251,
18977,0.3263,
18979,0.3765,
18980,0.4016,
18981,0.4267,
18982,0.4769,
18984,0.5523,
18985,0.5523,
18987,0.6025,
18988,0.6778,
18990,0.7029,
18991,0.7280,
18992,0.7782,
18993,0.8284,
18995,0.8535,
18996,0.9037,
18997,0.9288,
18998,0.9539,
19000,0.9790,
19001,1.0292,
19002,1.0794,
19003,1.0794,
19005,1.1045,
19006,1.1547,
19007,1.1547,
19008,1.2300,
19010,1.0292,
19011,1.3806,
19012,1.3053,
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

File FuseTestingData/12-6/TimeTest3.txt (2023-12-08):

43875,0.0000,
43876,0.0000,
43877,0.0000,
43879,1.1045,
43880,8.6604,
43881,8.6353,
43882,2.6860,
43884,8.4847,
43885,0.0000,
43886,0.0000,
43887,0.0000,
43888,0.0000,
43890,0.0000,
43891,0.0000,
43892,0.0000,
43893,0.0000,
43895,0.0000,
43896,0.0000,
43897,0.0000,
43898,0.0000,
43900,0.0000,
43901,0.0000,
43902,0.0000,
43904,0.0000,
43906,0.0000,
43907,0.0000,
43908,0.0000,
43909,0.0000,
43911,0.0000,
43912,0.0000,
43913,0.0000,
43914,0.0000,
43916,0.0000,
43917,0.0000,
43918,0.0000,
43919,0.0000,
43921,0.0000,
43922,0.3012,
43923,8.8110,
43924,8.7106,
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

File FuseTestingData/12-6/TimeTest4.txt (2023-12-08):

13775,0.0000,
13777,0.0000,
13778,0.0000,
13779,0.0251,
13780,0.0000,
13783,0.1757,
13784,0.1004,
13785,0.0000,
13786,0.0000,
13788,0.0753,
13789,0.0000,
13790,0.0753,
13791,0.0753,
13793,0.0753,
13794,0.0000,
13795,0.0000,
13796,0.0000,
13798,0.1255,
13799,0.0251,
13800,0.2259,
13801,0.1255,
13802,0.0000,
13804,0.1506,
13805,0.0000,
13806,0.0000,
13807,0.1255,
13809,0.0000,
13810,0.1004,
13811,0.0000,
13812,0.0000,
13814,0.0502,
13815,0.0000,
13816,0.0000,
13817,0.1757,
13819,0.1506,
13820,0.2008,
13821,0.0502,
13822,0.0000,
13825,0.1004,
13826,0.0000,
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

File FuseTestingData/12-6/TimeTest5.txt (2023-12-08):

12877,0.0000,
12878,0.0000,
12879,0.0000,
12880,0.0000,
12881,0.0000,
12883,0.0000,
12884,8.2336,
12886,7.9826,
12888,7.9575,
12889,8.0830,
12890,8.2336,
12891,8.3340,
12892,8.4847,
12894,8.6604,
12895,8.7859,
12896,8.8612,
12897,8.9114,
12899,8.9867,
12900,9.0369,
12901,9.0871,
12902,9.1373,
12904,9.1875,
12905,9.2377,
12906,9.2628,
12907,9.3130,
12909,9.3632,
12910,9.3883,
12911,9.4386,
12912,9.4637,
12914,9.5139,
12915,9.6143,
12916,9.8151,
12917,10.5682,
12919,12.5513,
12920,12.6015,
12921,12.6517,
12923,12.6768,
12924,12.7019,
12925,12.7270,
12928,12.7521,
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

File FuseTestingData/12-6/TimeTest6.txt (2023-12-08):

0.0000,
11058,0.0000,
11059,0.0000,
11060,0.0000,
11061,0.0000,
11063,0.0000,
11064,0.0000,
11065,0.0000,
11066,0.0000,
11068,0.0000,
11069,0.0000,
11070,0.0000,
11071,0.0000,
11073,0.0000,
11074,0.0000,
11075,0.0000,
11076,0.0000,
11078,0.0000,
11079,0.0000,
11080,0.0000,
11081,0.0000,
11083,0.0000,
11084,0.0000,
11085,0.0000,
11086,0.0000,
11088,0.0000,
11089,0.0000,
11090,0.0000,
11091,0.0000,
11094,0.0000,
11095,0.0000,
11096,0.0000,
11097,0.0000,
11099,0.0000,
11100,0.0000,
11101,0.0000,
11102,0.0000,
11104,0.0000,
11105,0.0000,
11106,0.0000,
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

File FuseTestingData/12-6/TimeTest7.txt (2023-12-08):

18,0.0000,
7319,0.0000,
7320,0.0000,
7322,0.0000,
7323,0.0000,
7324,0.0000,
7325,0.0000,
7326,0.0000,
7327,0.0000,
7329,0.0000,
7330,0.0000,
7331,0.0000,
7332,0.0000,
7333,0.0000,
7334,0.0000,
7336,0.0000,
7337,0.0000,
7339,0.0000,
7340,0.0000,
7341,0.0000,
7342,0.0000,
7344,0.0000,
7345,0.0000,
7346,0.0000,
7347,0.0000,
7348,0.0000,
7349,0.0000,
7351,0.0000,
7352,0.0000,
7353,0.0000,
7354,0.0000,
7355,0.0000,
7356,0.0000,
7357,0.0000,
7359,0.0000,
7360,0.0000,
7361,0.0000,
7362,0.0000,
7363,0.0000,
7364,0.0000,
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

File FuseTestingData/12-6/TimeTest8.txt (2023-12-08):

11599,0.0000,
11600,0.0000,
11601,0.0000,
11603,0.0000,
11604,0.0000,
11606,0.0000,
11607,0.0000,
11609,0.0000,
11610,0.0000,
11611,0.0000,
11612,0.0000,
11614,0.0000,
11615,0.0000,
11616,0.0000,
11617,0.0000,
11619,0.0000,
11620,0.0000,
11621,0.0000,
11622,0.0000,
11624,9.6645,
11625,8.7859,
11626,0.0000,
11627,0.0000,
11629,0.0000,
11630,0.0000,
11631,8.9867,
11632,8.7357,
11634,8.6855,
11635,8.8361,
11636,8.8361,
11637,8.8612,
11639,8.8863,
11640,8.9365,
11641,8.9867,
11642,9.0369,
11644,9.0871,
11645,9.1624,
11646,9.2377,
11648,9.3130,
11650,9.3381,
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

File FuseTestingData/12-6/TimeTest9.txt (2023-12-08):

10855,0.0000,
10856,0.0000,
10857,0.0000,
10858,0.0000,
10860,0.0000,
10861,0.0000,
10862,0.0000,
10863,0.0000,
10865,0.0000,
10866,0.0000,
10867,0.0000,
10868,0.0000,
10870,0.0000,
10871,0.0000,
10872,0.0000,
10873,0.0000,
10875,0.0000,
10876,0.0000,
10877,0.0000,
10878,0.0000,
10881,0.0000,
10882,0.0000,
10883,0.0000,
10884,0.0000,
10886,0.0000,
10887,0.0000,
10888,0.0000,
10889,8.9616,
10891,8.2336,
10892,0.0000,
10893,9.7900,
10894,8.7608,
10896,8.7357,
10897,8.8361,
10898,8.8110,
10899,8.8863,
10901,8.9114,
10902,8.9616,
10903,9.0369,
10904,9.0620,
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

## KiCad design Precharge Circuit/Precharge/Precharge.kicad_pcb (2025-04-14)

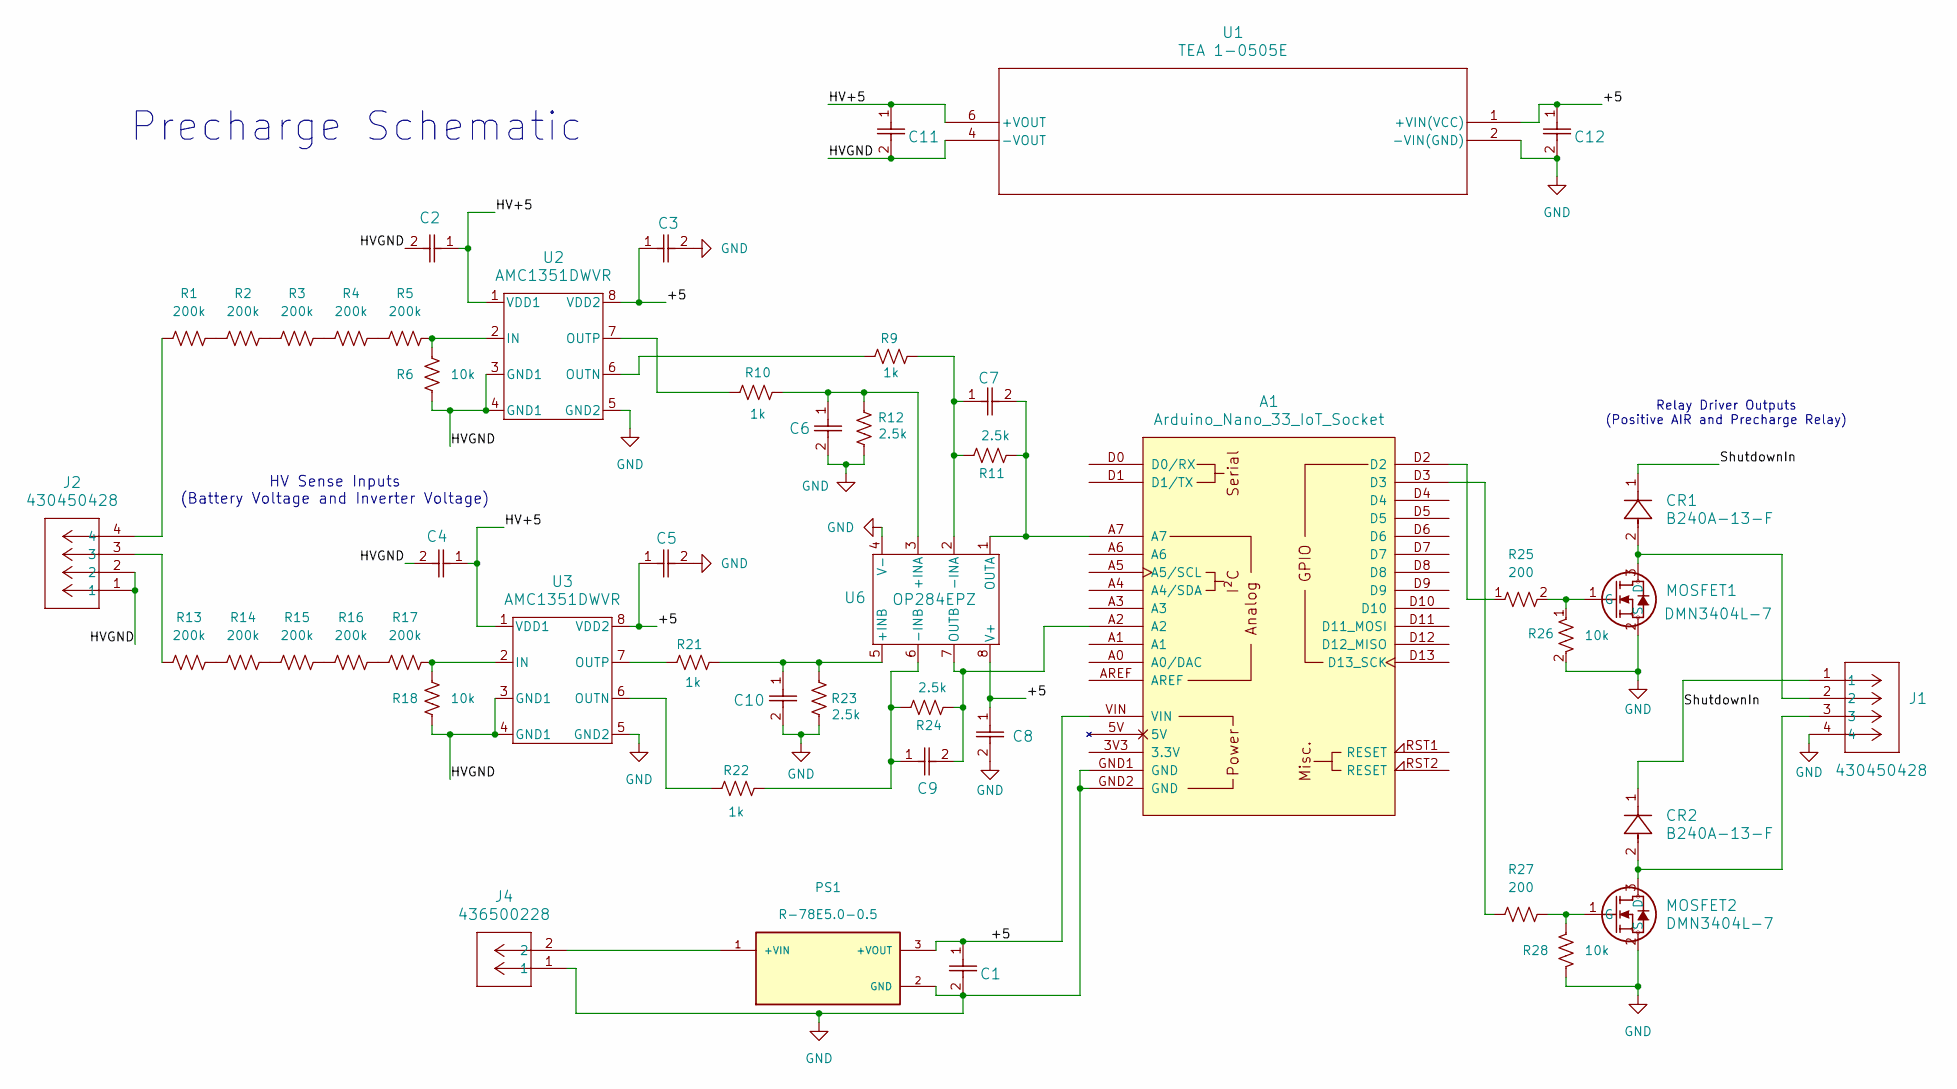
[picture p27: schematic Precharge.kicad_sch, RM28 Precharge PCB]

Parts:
A1: Arduino_Nano_33_IoT_Socket
C1, C11, C12: C324C106K3R5TA; CAP_C324C_MR_X7R_KEM
C2, C3, C4, C5, C8: K104K10X7RF5UH5; K104K10X7RF5UH5_VIS
C6, C7, C9, C10: K331K15X7RF5TL2; CAP_K-SERIES_15-L2_VIS
CR1, CR2: B240A-13-F; SMA_DIO-L
J1, J2: 430450428; CONN_SD-43045-010_04_MOL
J4: 436500228; CONN_SD-43650-010_02_MOL
MOSFET1, MOSFET2: DMN3404L-7; SOT23_DIO-L
PS1: R-78E5.0-0.5; CONV_R-78E5.0-0.5; PARTREV 4
R1, R2, R3, R4, R5, R13, R14, R15, R16, R17: 200k; R_Axial_DIN0207_L6.3mm_D2.5mm_P10.16mm_Horizontal
R6, R18, R26, R28: 10k; R_Axial_DIN0207_L6.3mm_D2.5mm_P10.16mm_Horizontal
R9, R10, R21, R22: 1k; R_Axial_DIN0207_L6.3mm_D2.5mm_P10.16mm_Horizontal
R11, R12, R23, R24: 2.5k; R_Axial_DIN0207_L6.3mm_D2.5mm_P10.16mm_Horizontal
R25, R27: 200; R_Axial_DIN0207_L6.3mm_D2.5mm_P10.16mm_Horizontal
U1: TEA 1-0505E; TEA 1E_TRP
U2, U3: AMC1351DWVR; SOIC8_DWV_TEX
U6: OP284EPZ; N_8_ADI

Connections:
/+5: A1.VIN, C1.1, C3.1, C5.1, C8.1, C12.1, PS1.3 (+VOUT), U1.1 (+VIN(VCC)), U2.8 (VDD2), U3.8 (VDD2), U6.8 (V+)
/HV+5: C2.1, C4.1, C11.1, U1.6 (+VOUT), U2.1 (VDD1), U3.1 (VDD1)
/HVGND: C2.2, C4.2, C11.2, J2.1, J2.2, R6.1, R18.1, U1.4 (-VOUT), U2.3 (GND1), U2.4 (GND1), U3.3 (GND1), U3.4 (GND1)
/ShutdownIn: CR1.1, CR2.1, J1.1
GND: A1.GND1 (GND), A1.GND2 (GND), C1.2, C3.2, C5.2, C6.2, C8.2, C10.2, C12.2, J1.4, J4.1, MOSFET1.2 (S), MOSFET2.2 (S), PS1.2 (GND), R12.1, R23.1, R26.2, R28.2, U1.2 (-VIN(GND)), U2.5 (GND2), U3.5 (GND2), U6.4 (V-)
unnamed: A1.D2, R25.1
unnamed: A1.D3, R27.1
unnamed: J2.3, R13.1
unnamed: J2.4, R1.1
unnamed: CR1.2, J1.2, MOSFET1.3 (D)
unnamed: MOSFET1.1 (G), R25.2, R26.1
unnamed: CR2.2, J1.3, MOSFET2.3 (D)
unnamed: MOSFET2.1 (G), R27.2, R28.1
unnamed: J4.2, PS1.1 (+VIN)
unnamed: R1.2, R2.1
unnamed: R2.2, R3.1
unnamed: R3.2, R4.1
unnamed: R4.2, R5.1
unnamed: R13.2, R14.1
unnamed: R14.2, R15.1
unnamed: R15.2, R16.1
unnamed: R16.2, R17.1
unnamed: R5.2, R6.2, U2.2 (IN)
unnamed: R9.1, U2.6 (OUTN)
unnamed: R10.1, U2.7 (OUTP)
unnamed: R17.2, R18.2, U3.2 (IN)
unnamed: R22.1, U3.6 (OUTN)
unnamed: R21.1, U3.7 (OUTP)
unnamed: C6.1, R10.2, R12.2, U6.3 (+INA)
unnamed: C10.1, R21.2, R23.2, U6.5 (+INB)
unnamed: C7.1, R9.2, R11.2, U6.2 (-INA)
unnamed: C9.1, R22.2, R24.2, U6.6 (-INB)
unnamed: A1.A7, C7.2, R11.1, U6.1 (OUTA)
unnamed: A1.A2, C9.2, R24.1, U6.7 (OUTB)

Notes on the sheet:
Precharge Schematic
HV Sense Inputs (Battery Voltage and Inverter Voltage)
Relay Driver Outputs (Positive AIR and Precharge Relay)

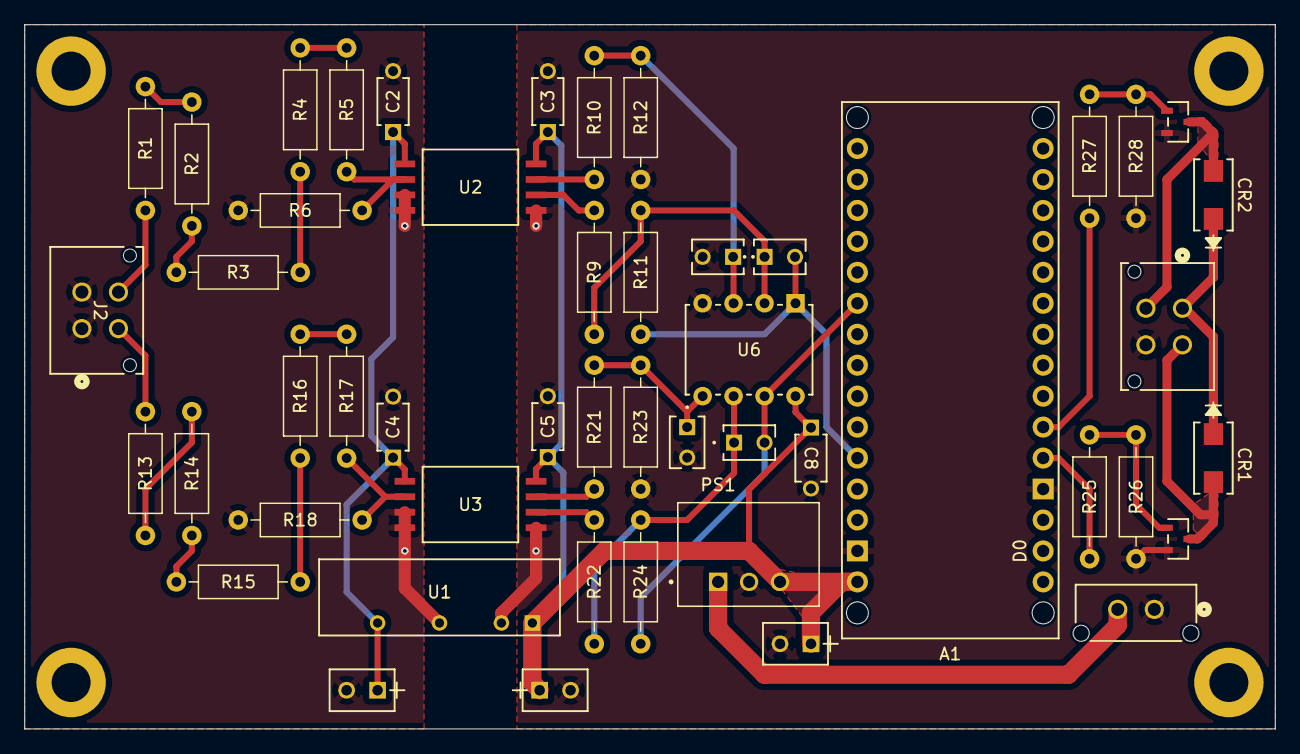
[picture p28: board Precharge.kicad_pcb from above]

Board: 2 copper layers, 102.6 x 57.8 mm, 49 parts (0 on the bottom side), 34 nets.

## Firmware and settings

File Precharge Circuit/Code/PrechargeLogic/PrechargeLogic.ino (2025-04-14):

#include <LibPrintf.h>

int HVpADC = A0;      // Analog Pin for reading HV+
int HVnADC = A1;      // Analog Pin for reading HV-
int VbattADC = A2;    // Analog Pin for reading Battery voltage
int HVpdig = 0;       // Positive but reading (digital)
int HVndig = 0;       // Negative bus reading (digital)
int HVdig = 0;        // Digital HV reading
//int HV = 0;           // Analog HV reading
int flag = 0;         // Used for setting precharge states
int Vref = 5;         // Max voltage the ADC can read
int ADCres = 1023;    // 10 bit ADC
int Vbattdig = 0;
int Vbatt = 0;

//float Conv = float(Vref)/float(ADCres);
float HVpA=0;
float HVnA=0;
float HVA=0;

void setup() {
  // put your setup code here, to run once:
  Serial.begin(9600);
}

void loop() {
  // put your main code here, to run repeatedly:
  readVoltage();
  /*
  while (flag = 0);
  while (flag = 1){
    SafetyCheck();
  }
  */
  //printf("Digital Measurments\r\nHVp: %u HVn: %u Final Value = %d\r\n",HVpdig, HVndig, HVdig);
  printf("Analog Measurements:\r\nHVp: %f HVn: %f Final Value = %f\r\n",HVpA, HVnA,HVA);
  //Serial.print("Serial digital value =");
  //Serial.print(HVpdig);
  //Serial.print("\r\n");
  delay(1000);
}

void readVoltage(){
  // Function outputs the tractive system voltage as a number between 0 and 1023 (resolution of the 10bit ADC)
  // Function also returns the HV reaing as an analog voltage
  // The positive and negative rails are read via ADCs, inverter voltage is calculated by subtractive HV- from HV+
  HVpdig = analogRead(HVpADC);
  HVndig = analogRead(HVnADC);
  HVdig = HVpdig-HVndig;
  Vbattdig = analogRead(VbattADC);
  Vbattdig = Vbattdig-HVndig;
  
  // Analog to digital value conversions
  // *Needs to be adjusted for voltage divider
  //HV = (Vref/ADCres)*HVdig;
  Vbatt = float(Vref)/float(ADCres)*float(Vbattdig);
  HVpA = (float(Vref)/float(ADCres)*float(HVpdig));
  HVnA = (float(Vref)/float(ADCres)*float(HVndig));
  HVA = (float(Vref)/float(ADCres)*float(HVdig));
}

/*
void SafetyCheck(void){
}
*/

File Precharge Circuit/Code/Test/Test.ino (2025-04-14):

/*****************************************************

              Prechage V1 Firmware
  
*****************************************************/
  
  int Vinvdig = 0;        // Tracks the inverter voltage (direct value from ADC)
  int Vbattdig = 0;       // Tracks the battery voltage (direct value from ADC)
  int VinvPIN = A2;       // Analog Pin for reading Inverter Voltage 
  int VbattPIN = A7;      // Analog Pin for reading Battery Voltage
  int RelayPIN = 3;       // CHEK LAURENS WIRING
  int AIRPIN = 2;         // CHECK LAURENS WIRING
  int State=0;            // Tracks the State of the Precharge board, State 0 is ready to precharge, State 1 is Precharged, State 3 is fault
  int Vdiff;
  int Vthresh = 500;



void setup() {
  Serial.begin(9600);     // For reading through Serial Monitor

  pinMode(RelayPIN,OUTPUT);   // Initialize Precharge Relay Pin 
  pinMode(AIRPIN,OUTPUT);
  digitalWrite(RelayPIN, HIGH);
}

void loop() {
  //digitalWrite(RelayPIN, LOW);
  //digitalWrite(AIRPIN,LOW);

  Vinvdig = analogRead(VinvPIN);
  Vbattdig = analogRead(VbattPIN);
  Vdiff = abs(Vinvdig-Vbattdig);

  if(Vbattdig<=Vthresh){
    digitalWrite(AIRPIN, LOW);
    digitalWrite(RelayPIN, LOW);
    State=3;
  }
  
  if (Vdiff>=0.05*Vinvdig && Vbattdig>Vthresh){
    digitalWrite(AIRPIN, LOW);
    digitalWrite(RelayPIN, HIGH);
    State=0;
  }
  if (Vdiff<=0.05*Vinvdig && Vinvdig>Vthresh){
    digitalWrite(AIRPIN, HIGH);
    State=1;
  }


  Serial.print("Vinv: ");
  Serial.print(Vinvdig);
  Serial.print("\n");
  Serial.print("Vbatt: ");
  Serial.print(Vbattdig);
  Serial.print("\n");
  Serial.print("State: ");
  Serial.print(State);
  Serial.print("\n");
  delay(100);
}

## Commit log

2023-12-02 Script for temperature rise of conductor over time
2023-12-08 More fusing data
    [TimeTest10.xlsx, TimeTest6.xlsx, TimeTest7.xlsx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]
2024-09-17 Fourier Analysis of Buck Converter
    Analysis of the 1st, 2nd, and 3rd harmonics of buck converter caused by switching.
2024-09-24 Preliminary Simulation for buck converter
    Controlled current charging of a battery cell.
2024-10-01 Added gate driver for simulation
    [Precharge Circuit.kicad_pcb, Precharge Circuit.kicad_sch]
2024-10-04 Working simulation for Synchronous Buck
2024-10-11 Improved battery model for output voltage simulation
    [LV.kicad_pcb, LV.kicad_sch]
2024-10-27 Working on Shudown Schmatic
    [LV.kicad_sch]
2024-10-27 Working on shutdown schematic
    [LV.kicad_sch, untitled.kicad_sch]
2024-10-29 Low-Pass Filter Simulation for PWM to Analog Conversion
2024-10-29 Update PWM to Analog Filter.asc
2024-11-02 PWM to Analog Filter with Op Amp Simulation
2024-11-08 Update to LV Schematic and move to different file structure
    [LV.kicad_pcb, LV.kicad_sch, Precharge Circuit.kicad_pcb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]
2024-11-17 Updated to KiCad 8.0 and continued work on shutdown circuit
    [untitled.kicad_sch]
2024-11-24 Started Precharge Schematic and Layout
    [Precharge.kicad_pcb, Precharge.kicad_sch]
2024-11-24 Updates to LV Schematic
    [LV.kicad_sch]
2024-12-07 Added Relay and Relay Driver to Schmatic/ Layout
    [Arduino v5.step]
2024-12-07 Added 3d Model for Arduino To Layout
    [Arduino Nano-STEP.STEP, SOT-23_TO-236_318_AT_OSI.step]
